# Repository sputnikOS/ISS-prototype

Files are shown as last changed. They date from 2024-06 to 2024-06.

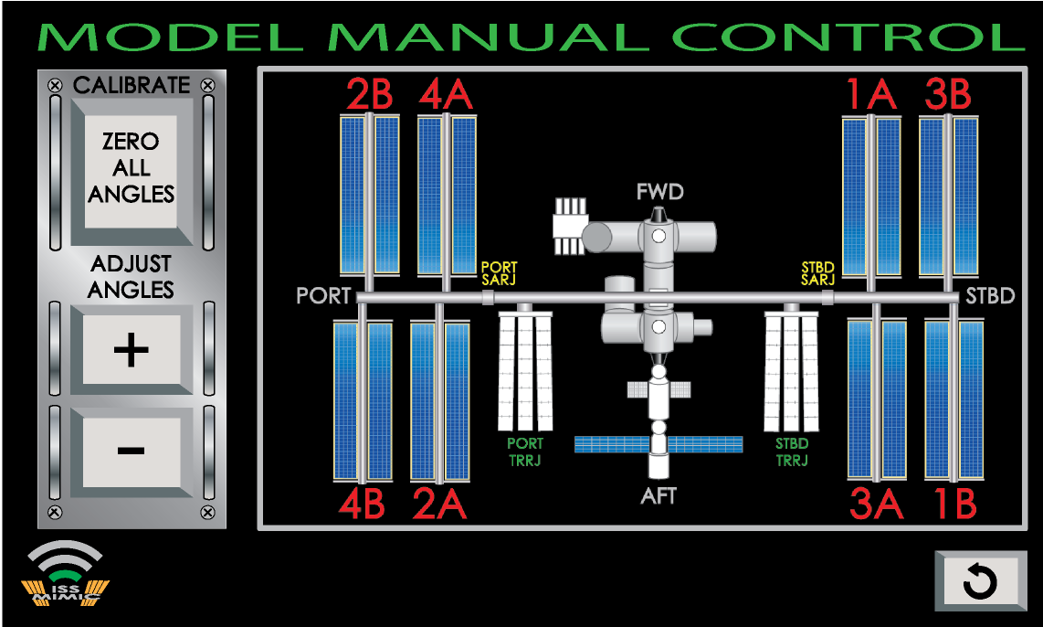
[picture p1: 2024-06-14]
Pi/imgs/calibrate/CalibrateExample.png

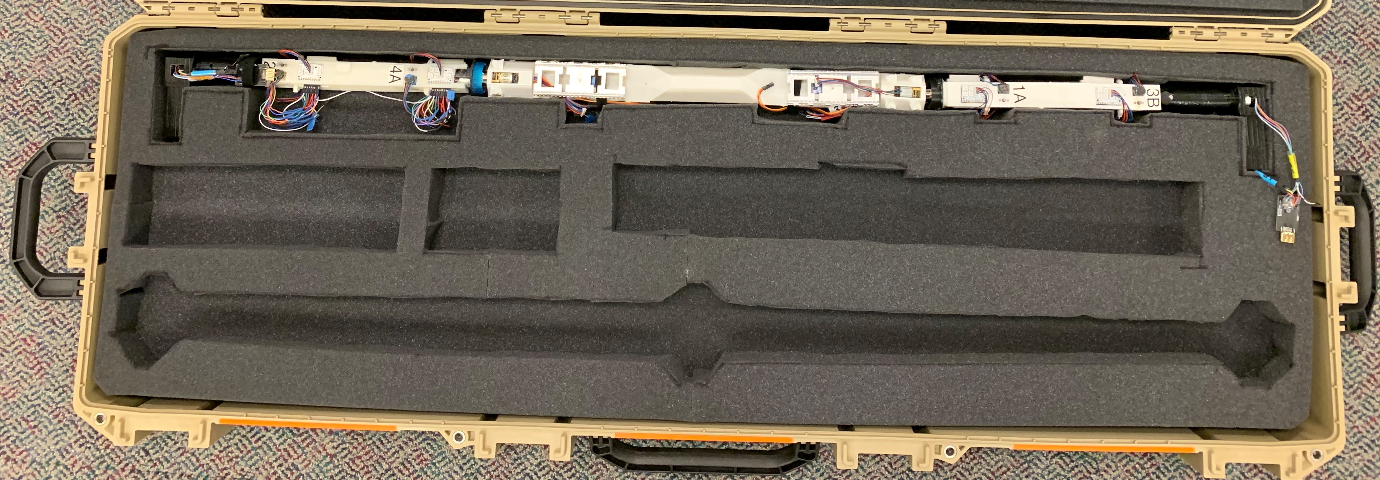
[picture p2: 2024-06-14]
Wiki/Images/Case_4_Main_Electronic_In.JPG

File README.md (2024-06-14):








Welcome to the ISS Mimic project repository! We are developing a 3D printed model of the International Space Station that uses the actual ISS live telemetry to mimic the actual positioning of the ISS solar arrays and radiators! We are also developing tools to visualize all of the ISS public telemetry in informative ways! Join our discord to provide feedback, ask questions, or get involved! 

https://discord.gg/zPKyE6hBSe

We are always looking for people to help with the coding of our raspberry pi telemetry display program, the telemetry website, the creation of ISS CAD models, general project ideas, etc... 

If you want to build your own ISS Mimic, or just want to use the ISS telemetry in your own application, we are more than happy to help. 

Check out our youtube video:

ISS MIMIC! (https://www.youtube.com/watch?v=W9iZBjzOEEQ)

ISS MIMIC!

The International Space Station is constantly downlinking data (telemetry) for Mission Control to monitor. Several years ago, NASA provided some of the data to the public in order to spur interest in the ISS and space exploration under the (now defunct) ISSlive project using the lightstreamer service (http://demos.lightstreamer.com/ISSLive/). We saw this project and wanted to expand on its potential. Since the development of isslive.com, some more data was added to the public feed and was, sadly, never incorporated into the website. The current total epic and all inclusive list of public telemetry can be seen at our page here https://iss-mimic.github.io/Mimic/ and in an even cooler format here https://iss-mimic.github.io/Mimic/dashboard.html Sadly, ISSlive.com is no longer maintained, but thanks largely in part to our efforts, the telemetry is still being provided to the public through the same lightstreamer connection. 

You can find info on installing our (still heavily in development but with some pretty cool working features now) custom ISS telemetry display program here: https://github.com/ISS-Mimic/Mimic/wiki/Build-Instruction%3A-Mimic-Software-Setup-Instructions

The telemetry is awesome in and of itself. But we wanted to do something more with the data, using it to drive software and hardware. Software - running a Raspberry Pi, we want to display all of the telemetry in an interesting and informative manner, enabling visualization of more than just boring numbers. Hardware - using Arduino related microcontrollers, receiving data from the Raspberry Pi, we want to control a 3D-printed model of the ISS and make it exactly match up with the actual ISS in real time. All of the solar arrays, radiators, and outboard truss will be able to rotate to match the ISS joint angles.

Stuff that moves

The project is still a work in progress. We have a fully functioning model that works with all 12 motors turning correctly and able to sync with live data. However, we want to increase the fidelity. Our low-fidelity model is completely finished and available here: [STL Files](https://github.com/ISS-Mimic/Mimic/tree/main/3D_Printing). We are still working on the high fidelity upgrade (help us!) and trying to make the ISS look as detailed as possible while still being printable. The software is still a work in progress, too. But from the standpoint of receiving telemetry and transmitting it to the Arduinos, the basic functionality is finished. The finishing touches on the software are all for visualizing the telemetry.

Functional but not pretty model!

DISCLAIMER - We are not professional programmers. We are just a group of dedicated ISS program employees and enthusiasts trying to share our love of the space program through this awesome project. All the code maintained here was created to work toward our specific goal, and much of it was using languages that none of us had used before. You may find the structure, style, and lack of comments to be completely novice and infuriating. You may scream out in frustration, laugh in disgust, or even weep at the obfuscated nonsense appearing before your eyes. 

That said, feel free to improve upon our caffeine-induced, late-night, insanity-plagued programming madness or even just scrap it all and make something better using our ideas.

Check out the wiki for more information.

You can view a video showing some of our project here:https://youtu.be/W9iZBjzOEEQ. Here's an older video: https://www.youtube.com/watch?v=sbdHXjDQ-U8 .

The software is pretty cool and provides even more in-depth functionality than isslive.com. We'll be adding videos and pictures soon to show off the software capabilities.

# Status/Priorities
We are currently focused on refining the CAD model and splitting out all the STL files for printing. All of the STL files currently in this repo are likely outdated or currently changing. We will also release the raw CAD once finished.

We are also working on finishing the software.

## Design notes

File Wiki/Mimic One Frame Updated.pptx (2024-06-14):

## Mimic One Frame Build Instruction (Example)

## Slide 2

FWD

2020 Vertical Supports (4)

Extruded 2040 Base

2020 Frame Supports (6)

Support Rods with Base (3)

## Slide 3

Step 1: Attach Frame Supports to 2040 Base (6 places)
2 small L-brackets each support, 2 Button Hex Screws each small L-bracket

Measurements are from centerline to centerline

2020 Frame Supports (6)

Frame Supports attached to 2040 Base by 2 small L-brackets using Button Hex Screws

Extruded 2040 Base

~610mm

~610mm

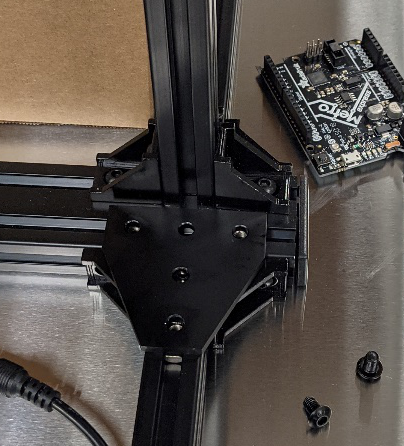
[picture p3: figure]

L-brackets

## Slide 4

Step 1a: Cut Rubber Strips for Frame Supports (6 places) and 2040 Base (both grooves)
Install Rubber Strips in the underside grooves of Frame Supports and 2040 Base.

The Rubber Strip provides friction with the table and to fill the space between the table and the Rubber Feet on the end of the Frame Supports.

2020 Frame Supports (6)

Extruded 2040 Base (both grooves)

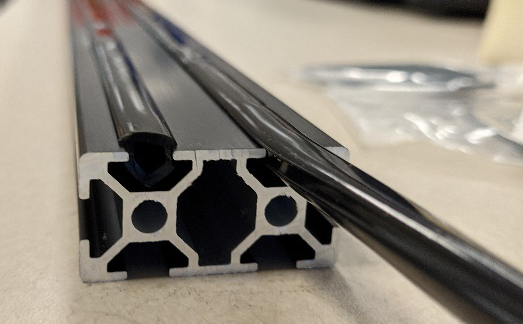
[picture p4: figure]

2040 Base shown upside down

Underside Groove

Rubber Strip

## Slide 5

Step 2: Install T-Plates on end Frame Supports in the rear groove of the 2040 (2 places)
1 T-plate per end Frame Support, 5 Button Hex Screws and T-nuts on each T-plate

2020 Frame Supports (6)

Frame Supports attached to 2040 Base by 2 small L-brackets and 1 T-plate using Button Hex Screws

Extruded 2040 Base

T-plate

L-brackets

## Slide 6

Step 3: Install T-Plates on center Frame Supports – one in forward groove, one in rear groove (2 places)
1 T-plate per center Frame Support, 5 Button Hex Screws and T-nuts on each T-plate

FWD

2020 Frame Supports (6)

Extruded 2040 Base

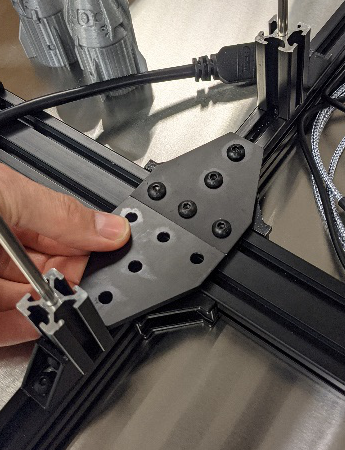
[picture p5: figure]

T-plates

Forward Groove in 2040

Rear Groove in 2040

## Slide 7

Vertical Supports (without T-plates) attached to forward groove with 2 small
L-brackets using
Button Hex screws

2020 Vertical Supports (4)

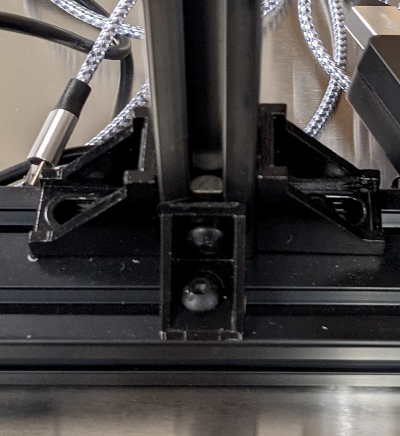
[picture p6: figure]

L-brackets

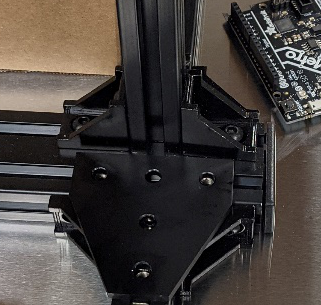
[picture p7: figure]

L-brackets

Vertical Supports attached to forward groove on 2040 Base by 2 small L-brackets using Button Hex Screws

Measurements are centerline to centerline.
Need to update: outside dimensions should be the same.

FWD

446mm

433mm

347mm

Extruded 2040 Base

Step 4: Attach Vertical Supports to forward groove in 2040 Base (4 places)
2 small L-brackets each support, 2 Button Hex Screws each small L-bracket

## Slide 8

Vertical Supports (without T-plates) attached to forward groove with 2 small
L-brackets and 1
L-bracket anchored in rear groove

2020 Vertical Supports (4)

Step 5: Add 1 large L-bracket anchored in rear groove in 2040 Base on center supports(2 places)
1 large L-bracket each support, 2 Button Hex Screws each small L-bracket

FWD

Extruded 2040 Base

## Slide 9

Step 6: Support Rod Bases on center Frame Supports (3 places)
1 large L-bracket per Support Rod Base, 2 Button Hex Screws each L-bracket

2020 Frame Supports (6)

160mm

243mm

Extruded 2040 Base

L-brackets

Vertical 2020 is flush
with end of the horizontal 2020

Support Rods with Base (3)

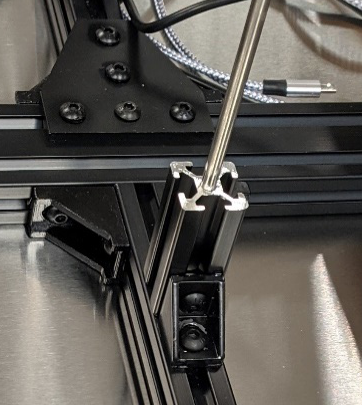
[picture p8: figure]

Support Rod Base attached to 2020 Frame Support by 1 large
L-bracket using Button Hex Screws

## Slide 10

Step 7: Install Rubber Feet on Support Rod Bases (3 places)
Rubber Feet finish off ends of extruded Support Rod Bases and provide additional support with rods

Note, a cut will need to be made or a small hole drilled to allow Support Rod to pass through – hole must be smaller than rod to provide friction for extra stability

2020 Frame Supports (6)

Extruded 2040 Base

Add new photo with rubber

Rubber Feet on Support Rod Base

Support Rods with Base (3)

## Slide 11

Step 8: Insert Support Rods in Support Rod Bases (3 places)
Support Rod will drop down into groove of Frame Support

2020 Frame Supports (6)

Extruded 2040 Base

Add new photo with rubber

Support Rod inserted through Rubber Feet into Support Rod Base

Support Rods with Base (3)

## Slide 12

Step 9: Install Rubber Feet on Frame Supports (6 places)
Rubber Feet finish off ends of Frame Supports and provide friction with table

2020 Frame Supports (6)

Extruded 2040 Base

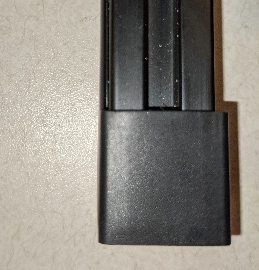
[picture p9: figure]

Support Rods with Base (3)

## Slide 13

Step 10: Install End Caps on 2040 Base ends (2 places)
End Caps finish off ends of 2040 Base

Extruded 2040 Base

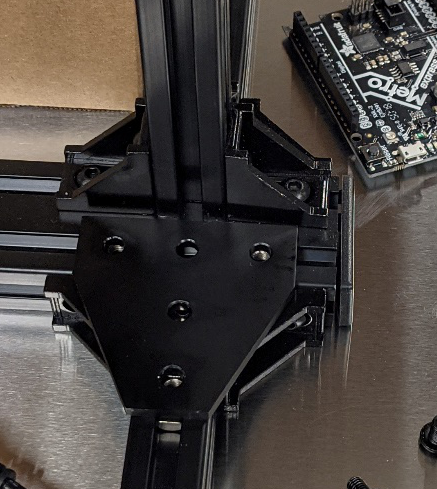
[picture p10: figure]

End Cap (2) inserted into end of 2040 Base

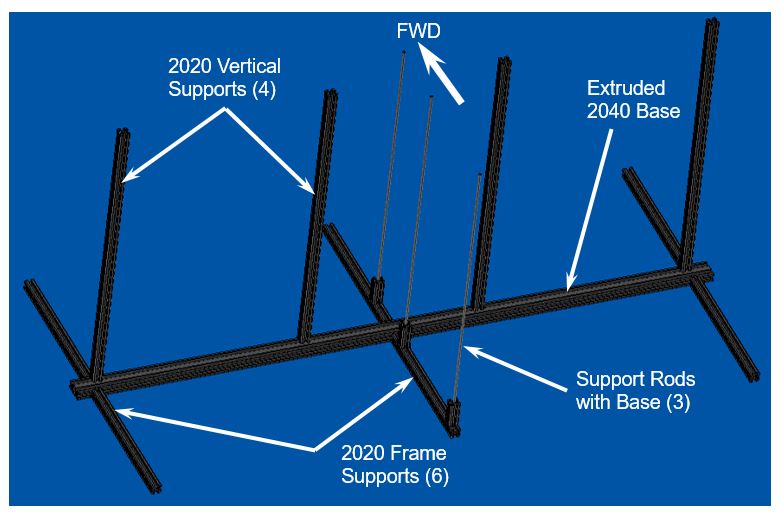
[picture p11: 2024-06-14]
Wiki/Images/FrameOverview.JPG

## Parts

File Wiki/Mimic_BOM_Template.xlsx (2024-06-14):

 |  |  |  |  |  |  |  | output string - copy everything below in this column for the markdown file |  |  |  |  |  |  |  |  | concats
 |  |  |  |  |  |  |  | ### Raspberry Pi / Mimic Control Unit
 |  |  |  |  |  |  |  | | **Part** | **Quantity** | **Cost Per Unit** | **Total Cost** | **URL** | **Notes** | **Image**
Part | Quantity | Cost Per Unit | Total Cost | Part URL Name | Part URL | Notes | Image URL | | --- | :--: | :--: | :--: | --- | --- | ---
4GB Raspberry Pi 4 | 1 | $67.79 | $67.79 | Amazon | https://www.amazon.com/dp/B07TC2BK1X | Might work with the 1GB/2GB versions but not guaranteed | https://images-na.ssl-images-amazon.com/images/I/71RJj8SmQGL._SL1500_.jpg | | 4GB Raspberry Pi 4 | 1 | $67.79 | $67.79 | [Amazon](https://www.amazon.com/dp/B07TC2BK1X) | Might work with the 1GB/2GB versions but not guaranteed | <img src="https://images-na.ssl-images-amazon.com/images/I/71RJj8SmQGL._SL1500_.jpg" width="200">
Power Supply | 1 | $9.99 | $9.99 | Amazon | https://www.amazon.com/gp/product/B097P2NLVH/ | Need at least 2.4 amp power supply | https://m.media-amazon.com/images/I/610tc+KJ17S._AC_SL1500_.jpg | | Power Supply | 1 | $9.99 | $9.99 | [Amazon](https://www.amazon.com/gp/product/B097P2NLVH/) | Need at least 2.4 amp power supply | <img src="https://m.media-amazon.com/images/I/610tc+KJ17S._AC_SL1500_.jpg" width="200">
MicroSD Card | 1 | $8.98 | $8.98 | Amazon | https://www.amazon.com/SanDisk-Ultra-microSDXC-Memory-Adapter/dp/B073JWXGNT | Recommend 32GB, you'll also need a microSD card reader | https://images-na.ssl-images-amazon.com/images/I/81ClkOh2gpL._SL1500_.jpg | | MicroSD Card | 1 | $8.98 | $8.98 | [Amazon](https://www.amazon.com/SanDisk-Ultra-microSDXC-Memory-Adapter/dp/B073JWXGNT) | Recommend 32GB, you'll also need a microSD card reader | <img src="https://images-na.ssl-images-amazon.com/images/I/81ClkOh2gpL._SL1500_.jpg" width="200">
Raspberry Pi Official Touchscreen | 1 | $92.81 | $92.81 | Amazon | https://www.amazon.com/Raspberry-Pi-7-Touchscreen-Display/dp/B0153R2A9I/ | Possible to use other screens but the program was designed for this one | https://images-na.ssl-images-amazon.com/images/I/51Fju0ie9sL._SL1000_.jpg | | Raspberry Pi Official Touchscreen | 1 | $92.81 | $92.81 | [Amazon](https://www.amazon.com/Raspberry-Pi-7-Touchscreen-Display/dp/B0153R2A9I/) | Possible to use other screens but the program was designed for this one | <img src="https://images-na.ssl-images-amazon.com/images/I/51Fju0ie9sL._SL1000_.jpg" width="200">
Raspberry Pi/Touchscreen Case (optional) | 1 | $29.99 | $29.99 | Amazon | https://www.amazon.com/SmartiPi-Touch-Official-Raspberry-Touchscreen/dp/B07WXK38YM/ | This is the best Raspi Case but again not strictly required | https://images-na.ssl-images-amazon.com/images/I/71P7ThIhIRL._SL1500_.jpg | | Raspberry Pi/Touchscreen Case (optional) | 1 | $29.99 | $29.99 | [Amazon](https://www.amazon.com/SmartiPi-Touch-Official-Raspberry-Touchscreen/dp/B07WXK38YM/) | This is the best Raspi Case but again not strictly required | <img src="https://images-na.ssl-images-amazon.com/images/I/71P7ThIhIRL._SL1500_.jpg" width="200">
4-Port Powered USB Hub | 1 | $19.99 | $19.99 | Amazon | https://www.amazon.com/gp/product/B00TPMEOYM/ | Any powered hub should work, but this is the one we for which we've designed a mount | https://m.media-amazon.com/images/I/71fOD0-BRQL._AC_SL1500_.jpg | | 4-Port Powered USB Hub | 1 | $19.99 | $19.99 | [Amazon](https://www.amazon.com/gp/product/B00TPMEOYM/) | Any powered hub should work, but this is the one we for which we've designed a mount | <img src="https://m.media-amazon.com/images/I/71fOD0-BRQL._AC_SL1500_.jpg" width="200">
USB-A to USB-Micro B data cables | 1 | $11.99 | $11.99 | Amazon | https://www.amazon.com/gp/product/B011KLFERG/ | Four cables required. You can use old phone cables, but make sure they support data transfer, not just charging | https://m.media-amazon.com/images/I/81z7vkDJTdL._AC_SL1500_.jpg | | USB-A to USB-Micro B data cables | 1 | $11.99 | $11.99 | [Amazon](https://www.amazon.com/gp/product/B011KLFERG/) | Four cables required. You can use old phone cables, but make sure they support data transfer, not just charging | <img src="https://m.media-amazon.com/images/I/81z7vkDJTdL._AC_SL1500_.jpg" width="200">
Mini Wireless Keyboard + Mouse (optional) | 1 | $29.95 | $29.95 | Amazon | https://www.amazon.com/gp/product/B011KPIZ9G/ | Use whatever mouse + keyboard you like, we like how this is a mouse and keyboard, portable and only uses one USB port | https://images-na.ssl-images-amazon.com/images/I/41YUr5YjuFL._AC_.jpg | | Mini Wireless Keyboard + Mouse (optional) | 1 | $29.95 | $29.95 | [Amazon](https://www.amazon.com/gp/product/B011KPIZ9G/) | Use whatever mouse + keyboard you like, we like how this is a mouse and keyboard, portable and only uses one USB port | <img src="https://images-na.ssl-images-amazon.com/images/I/41YUr5YjuFL._AC_.jpg" width="200">
USB Battery Pack (optional) | 1 | $49.95 | $49.95 | Amazon | https://www.amazon.com/Anker-PowerCore-Technology-High-Capacity-Compatible/dp/B07S829LBX/ | If you want to have a portable power option for the Raspberry Pi Station, this is a good option | https://images-na.ssl-images-amazon.com/images/I/71PYhWFaWEL._AC_SL1500_.jpg | | USB Battery Pack (optional) | 1 | $49.95 | $49.95 | [Amazon](https://www.amazon.com/Anker-PowerCore-Technology-High-Capacity-Compatible/dp/B07S829LBX/) | If you want to have a portable power option for the Raspberry Pi Station, this is a good option | <img src="https://images-na.ssl-images-amazon.com/images/I/71PYhWFaWEL._AC_SL1500_.jpg" width="200">
 |  |  |  |  |  |  |  | | **Subtotal** | **Subtotal + Keyboard & Battery**
 |  |  |  |  |  |  |  | | :---: | :---:
 |  | $241.54 | $321.44 |  |  |  |  | | $241.54 | $321.44
 |  |  |  |  |  |  |  | ### Essential Parts
 |  |  |  |  |  |  |  | | **Part** | **Quantity** | **Cost Per Unit** | **Total Cost** | **URL** | **Notes** | **Image**
Part | Quantity | Cost Per Unit | Total Cost | Part URL Name | Part URL | Notes | Image URL | | --- | :--: | :--: | :--: | --- | --- | ---
175 RPM Micro Gear Motor w/Encoder | 10 | $19.99 | $199.90 | Amazon | https://www.amazon.com/175-RPM-Micro-Gearmotor-Encoder/dp/B0195C9GSU | Motor for SARJs + BGAs | https://github.com/ISS-Mimic/Mimic/blob/main/Wiki/Images/DCmotor.png | | 175 RPM Micro Gear Motor w/Encoder | 10 | $19.99 | $199.9 | [Amazon](https://www.amazon.com/175-RPM-Micro-Gearmotor-Encoder/dp/B0195C9GSU) | Motor for SARJs + BGAs | <img src="https://github.com/ISS-Mimic/Mimic/blob/main/Wiki/Images/DCmotor.png" width="200">
Motor mount screws | 1 | $9.54 | $9.54 | McMasterCarr | https://www.mcmaster.com/92010A779/ | Mounts motors in place. M1.6x4mm flat head hex screw (100 pack). Total of 20 screws required. | https://github.com/ISS-Mimic/Mimic/blob/main/Wiki/Images/mmc_screw.png | | Motor mount screws | 1 | $9.54 | $9.54 | [McMasterCarr](https://www.mcmaster.com/92010A779/) | Mounts motors in place. M1.6x4mm flat head hex screw (100 pack). Total of 20 screws required. | <img src="https://github.com/ISS-Mimic/Mimic/blob/main/Wiki/Images/mmc_screw.png" width="200">
Couplers to Mount Solar Arrays on the motors | 1 | $10.99 | $10.99 | Amazon | https://www.amazon.com/Befenybay-Connector-Copper-Flexible-Coupling/dp/B07VFFJBVH/ | (8 Pcs) 3mm to 3mm Brass Connector Copper | https://images-na.ssl-images-amazon.com/images/I/71Gfh5ie8ML._AC_SX679_.jpg | | Couplers to Mount Solar Arrays on the motors | 1 | $10.99 | $10.99 | [Amazon](https://www.amazon.com/Befenybay-Connector-Copper-Flexible-Coupling/dp/B07VFFJBVH/) | (8 Pcs) 3mm to 3mm Brass Connector Copper | <img src="https://images-na.ssl-images-amazon.com/images/I/71Gfh5ie8ML._AC_SX679_.jpg" width="200">
Replacement Set Screws for Solar Array Couplers | 1 | $3.50 | $3.50 | McMaster | https://www.mcmaster.com/92605A100/ | M3 x 6mm Long Stainless Steel Flat-Tip Set Screw (Pkg of 25) | https://github.com/ISS-Mimic/Mimic/blob/main/Wiki/Images/mmc_setscrew.png | | Replacement Set Screws for Solar Array Couplers | 1 | $3.5 | $3.5 | [McMaster](https://www.mcmaster.com/92605A100/) | M3 x 6mm Long Stainless Steel Flat-Tip Set Screw (Pkg of 25) | <img src="https://github.com/ISS-Mimic/Mimic/blob/main/Wiki/Images/mmc_setscrew.png" width="200">
Pinion Gear to work with printed SARJ Ring | 2 | $9.70 | $19.40 | Amazon | https://www.amazon.com/Traxxas-3942X-Hardened-12-Tooth-Pinion/dp/B078KFCN72 | Traxxas 3942X 12-T Pinion Gear, 32P | https://m.media-amazon.com/images/I/41lWRhK7rWS._AC_SL1400_.jpg | | Pinion Gear to work with printed SARJ Ring | 2 | $9.7 | $19.4 | [Amazon](https://www.amazon.com/Traxxas-3942X-Hardened-12-Tooth-Pinion/dp/B078KFCN72) | Traxxas 3942X 12-T Pinion Gear, 32P | <img src="https://m.media-amazon.com/images/I/41lWRhK7rWS._AC_SL1400_.jpg" width="200">
Slip Ring | 4 | $21.00 | $84.00 | Amazon | https://www.amazon.com/GeeBat-Capsule-Electrical-CIRCUITSx2A-equipment/dp/B01N63E1N3 | Slip Ring - 12 Wires with Flange | https://images-na.ssl-images-amazon.com/images/I/71P8F3tKd3L._AC_SX679_.jpg | | Slip Ring | 4 | $21 | $84 | [Amazon](https://www.amazon.com/GeeBat-Capsule-Electrical-CIRCUITSx2A-equipment/dp/B01N63E1N3) | Slip Ring - 12 Wires with Flange | <img src="https://images-na.ssl-images-amazon.com/images/I/71P8F3tKd3L._AC_SX679_.jpg" width="200">
Motor Driver Shield | 3 | $23.99 | $71.97 | Amazon | https://www.amazon.com/gp/product/B073SP76MC/ | HiLetgo TB6612 Mosfet for Arduino Motor Shield | https://m.media-amazon.com/images/I/61w0lRDnX5L._AC_SL1010_.jpg | | Motor Driver Shield | 3 | $23.99 | $71.97 | [Amazon](https://www.amazon.com/gp/product/B073SP76MC/) | HiLetgo TB6612 Mosfet for Arduino Motor Shield | <img src="https://m.media-amazon.com/images/I/61w0lRDnX5L._AC_SL1010_.jpg" width="200">
Adafruit Metro M0 | 4 | $36.95 | $147.80 | Amazon | https://www.amazon.com/Adafruit-3505-Metro-Express-CircuitPython/dp/B071P145RG/ | Adafruit (PID 3505 Metro M0 Express - Designed for CircuitPython - ATSAMD21G18 | https://images-na.ssl-images-amazon.com/images/I/811K-LHnsoL._AC_SL1200_.jpg | | Adafruit Metro M0 | 4 | $36.95 | $147.8 | [Amazon](https://www.amazon.com/Adafruit-3505-Metro-Express-CircuitPython/dp/B071P145RG/) | Adafruit (PID 3505 Metro M0 Express - Designed for CircuitPython - ATSAMD21G18 | <img src="https://images-na.ssl-images-amazon.com/images/I/811K-LHnsoL._AC_SL1200_.jpg" width="200">
Servo Motors for Radiators | 1 | $9.99 | $9.99 | Amazon | https://www.amazon.com/Micro-Servos-Helicopter-Airplane-Controls/dp/B07MLR1498/ | TowerPro SG90 Servo (2 required, 4 in this pack) | https://images-na.ssl-images-amazon.com/images/I/61EX8cfTXRL._AC_SL1200_.jpg | | Servo Motors for Radiators | 1 | $9.99 | $9.99 | [Amazon](https://www.amazon.com/Micro-Servos-Helicopter-Airplane-Controls/dp/B07MLR1498/) | TowerPro SG90 Servo (2 required, 4 in this pack) | <img src="https://images-na.ssl-images-amazon.com/images/I/61EX8cfTXRL._AC_SL1200_.jpg" width="200">
Jumper Wires for Motor and Mimic Shields | 1 | $6.98 | $6.98 | Amazon | https://www.amazon.com/gp/product/B01EV70C78/ (https://smile.amazon.com/gp/product/B01EV70C78/) | 20cm Assorted Breadboard Jumper Wires | https://m.media-amazon.com/images/I/81lyrrBqMIL._AC_SL1500_.jpg | | Jumper Wires for Motor and Mimic Shields | 1 | $6.98 | $6.98 | [Amazon](https://www.amazon.com/gp/product/B01EV70C78/) | 20cm Assorted Breadboard Jumper Wires | <img src="https://m.media-amazon.com/images/I/81lyrrBqMIL._AC_SL1500_.jpg" width="200">
12V/5A Power Supply for Motors | 1 | $12.99 | $12.99 | Amazon | https://www.amazon.com/gp/product/B01461MOGQ (https://smile.amazon.com/gp/product/B01461MOGQ) | LEDMO Power Supply | https://m.media-amazon.com/images/I/51a0PcZlVkL._AC_.jpg | | 12V/5A Power Supply for Motors | 1 | $12.99 | $12.99 | [Amazon](https://www.amazon.com/gp/product/B01461MOGQ) | LEDMO Power Supply | <img src="https://m.media-amazon.com/images/I/51a0PcZlVkL._AC_.jpg" width="200">
Inline On/Off Switch (Optional) | 1 | $9.99 | $9.99 | Amazon | https://www.amazon.com/AWADUO-Extension-Adapter-Connector-Security/dp/B0B4638FG | JEEUE 12V Power DC Male to Female Cable with On/Off Switch | https://m.media-amazon.com/images/I/51istd+aMsL._SL1000_.jpg | | Inline On/Off Switch (Optional) | 1 | $9.99 | $9.99 | [Amazon](https://www.amazon.com/AWADUO-Extension-Adapter-Connector-Security/dp/B0B4638FG) | JEEUE 12V Power DC Male to Female Cable with On/Off Switch | <img src="https://m.media-amazon.com/images/I/51istd+aMsL._SL1000_.jpg" width="200">
DC Power Splitter Cable | 1 | $8.99 | $8.99 | Amazon | https://www.amazon.com/gp/product/B06Y5G3CMJ (https://smile.amazon.com/gp/product/B06Y5G3CMJ) | DZYDZR 3pcs 5.5mm x 2.1mm Y Splitter Cable 1 Female to 3 Male Splitter | https://m.media-amazon.com/images/I/61rz64AJ-KL._AC_SL1000_.jpg | | DC Power Splitter Cable | 1 | $8.99 | $8.99 | [Amazon](https://www.amazon.com/gp/product/B06Y5G3CMJ) | DZYDZR 3pcs 5.5mm x 2.1mm Y Splitter Cable 1 Female to 3 Male Splitter | <img src="https://m.media-amazon.com/images/I/61rz64AJ-KL._AC_SL1000_.jpg" width="200">
DC Power Plug Pigtail | 1 | $8.43 | $8.43 | Amazon | https://www.amazon.com/gp/product/B01M0EAR9N (https://smile.amazon.com/gp/product/B01M0EAR9N) | DC Power Plug Pigtail Cable (Female Power Plug Pigtail Cable / 19.68 inches/Pack of 10) | https://m.media-amazon.com/images/I/71WZivU7NpL._AC_SL1500_.jpg | | DC Power Plug Pigtail | 1 | $8.43 | $8.43 | [Amazon](https://www.amazon.com/gp/product/B01M0EAR9N) | DC Power Plug Pigtail Cable (Female Power Plug Pigtail Cable / 19.68 inches/Pack of 10) | <img src="https://m.media-amazon.com/images/I/71WZivU7NpL._AC_SL1500_.jpg" width="200">
Velcro Cable Ties (optional) | 1 | $6.99 | $6.99 | Amazon | https://www.amazon.com/gp/product/B00O9VKVFK (https://smile.amazon.com/gp/product/B00O9VKVFK) | Attmu 50 PCS Reusable Fastening Cable Ties | https://m.media-amazon.com/images/I/719z+1KonvL._AC_SL1500_.jpg | | Velcro Cable Ties (optional) | 1 | $6.99 | $6.99 | [Amazon](https://www.amazon.com/gp/product/B00O9VKVFK) | Attmu 50 PCS Reusable Fastening Cable Ties | <img src="https://m.media-amazon.com/images/I/719z+1KonvL._AC_SL1500_.jpg" width="200">
HDMI Cables (Generic) | 3 | $10.99 | $32.97 | Amazon | https://www.amazon.com/gp/product/B07LFN7CX6 | Any standard HDMI cable should work | https://m.media-amazon.com/images/I/610Y4RHIzRL._AC_SL1200_.jpg | | HDMI Cables (Generic) | 3 | $10.99 | $32.97 | [Amazon](https://www.amazon.com/gp/product/B07LFN7CX6) | Any standard HDMI cable should work | <img src="https://m.media-amazon.com/images/I/610Y4RHIzRL._AC_SL1200_.jpg" width="200">
 |  |  |  |  |  |  |  | | **Subtotal**
 |  |  |  |  |  |  |  | | :---:
 |  |  | $644.43 |  |  |  |  | | $644.43
 |  |  |  |  |  |  |  | ### Modelling (3D Printing/Module Connections/Aesthetics)
 |  |  |  |  |  |  |  | | **Part** | **Quantity** | **Cost Per Unit** | **Total Cost** | **URL** | **Notes** | **Image**
Part | Quantity | Cost Per Unit | Total Cost | Part URL Name | Part URL | Notes | Image URL | | --- | :--: | :--: | :--: | --- | --- | ---
3D Printer PLA Filament | 1 | $24.99 | $24.99 | Amazon | https://www.amazon.com/gp/product/B0B2NZZXLX | 3D Printer Filament, Polymaker White - be sure to get the proper diameter filament for your printer (feel free to use whatever filament) | https://m.media-amazon.com/images/I/71etInNZiSL._AC_SL1500_.jpg | | 3D Printer PLA Filament | 1 | $24.99 | $24.99 | [Amazon](https://www.amazon.com/gp/product/B0B2NZZXLX) | 3D Printer Filament, Polymaker White - be sure to get the proper diameter filament for your printer (feel free to use whatever filament) | <img src="https://m.media-amazon.com/images/I/71etInNZiSL._AC_SL1500_.jpg" width="200">
Ring Magnets for Module Connecting - lightweight | 60 | $0.52 | $31.20 | KJ Magnetics | https://www.kjmagnetics.com/proddetail.asp?prod=R841 | ½”OD x 1/4”ID x 1/16”thick ring magnets | https://www.kjmagnetics.com/prodimages2/1280/R841one.jpg | | Ring Magnets for Module Connecting - lightweight | 60 | $0.52 | $31.2 | [KJ Magnetics](https://www.kjmagnetics.com/proddetail.asp?prod=R841) | ½”OD x 1/4”ID x 1/16”thick ring magnets | <img src="https://www.kjmagnetics.com/prodimages2/1280/R841one.jpg" width="200">
Ring Magnets for Module Connecting - Heavyweight | 10 | $1.04 | $10.40 | KJ Magnetics | https://www.kjmagnetics.com/proddetail.asp?prod=R842-N52 | ½”OD x 1/4”ID x 1/8” thick ring magnets | https://www.kjmagnetics.com/prodimages2/1280/R842-N52one.jpg | | Ring Magnets for Module Connecting - Heavyweight | 10 | $1.04 | $10.4 | [KJ Magnetics](https://www.kjmagnetics.com/proddetail.asp?prod=R842-N52) | ½”OD x 1/4”ID x 1/8” thick ring magnets | <img src="https://www.kjmagnetics.com/prodimages2/1280/R842-N52one.jpg" width="200">
Cylinder Magnets for TBD | 2 | $1.40 | $2.80 | KJ Magnetics | https://www.kjmagnetics.com/proddetail.asp?prod=D12-N52 | 1/16”diam x 1/8” thick cylinder magnets | https://www.kjmagnetics.com/prodimages2/1280/D12-N52one.jpg | | Cylinder Magnets for TBD | 2 | $1.4 | $2.8 | [KJ Magnetics](https://www.kjmagnetics.com/proddetail.asp?prod=D12-N52) | 1/16”diam x 1/8” thick cylinder magnets | <img src="https://www.kjmagnetics.com/prodimages2/1280/D12-N52one.jpg" width="200">
Support Rods for Inboard Truss Segment | 2 | $2.54 | $5.08 | McMaster | https://www.mcmaster.com/98861A040/ | M3 Steel Threaded Rod, 1-m Long | https://github.com/ISS-Mimic/Mimic/blob/main/Wiki/Images/mmc_nut.png | | Support Rods for Inboard Truss Segment | 2 | $2.54 | $5.08 | [McMaster](https://www.mcmaster.com/98861A040/) | M3 Steel Threaded Rod, 1-m Long | <img src="https://github.com/ISS-Mimic/Mimic/blob/main/Wiki/Images/mmc_nut.png" width="200">
M3 Locknuts | 1 | $4.65 | $4.65 | McMaster | https://www.mcmaster.com/90576A102/ | M3 Steel Nylon-Insert Locknut (Pkg 100) | https://github.com/ISS-Mimic/Mimic/blob/main/Wiki/Images/mmc_threadedrod.png | | M3 Locknuts | 1 | $4.65 | $4.65 | [McMaster](https://www.mcmaster.com/90576A102/) | M3 Steel Nylon-Insert Locknut (Pkg 100) | <img src="https://github.com/ISS-Mimic/Mimic/blob/main/Wiki/Images/mmc_threadedrod.png" width="200">
Bamboo Skewers for attaching module halves | 1 | $5.99 | $5.99 | Amazon | https://www.amazon.com/Appetiser-Cocktail-Chocolate-Fountain-Barbecue/dp/B07MY7XVB1/ | HOPELF 6" Natural Bamboo Skewers, Φ=4mm (100 pcs) | https://m.media-amazon.com/images/I/61MhlR2cAtL._AC_SL1500_.jpg | | Bamboo Skewers for attaching module halves | 1 | $5.99 | $5.99 | [Amazon](https://www.amazon.com/Appetiser-Cocktail-Chocolate-Fountain-Barbecue/dp/B07MY7XVB1/) | HOPELF 6" Natural Bamboo Skewers, Φ=4mm (100 pcs) | <img src="https://m.media-amazon.com/images/I/61MhlR2cAtL._AC_SL1500_.jpg" width="200">
Cyanoacrylate Glue | 1 | $9.49 | $9.49 | Amazon | https://www.amazon.com/Gorilla-105801-Super-1-Pack-Clear/dp/B08QR2XRKD | Gorilla Super Glue Gel (any "superglue" should work) | https://m.media-amazon.com/images/I/81kAtvCkeBS._AC_SL1500_.jpg | | Cyanoacrylate Glue | 1 | $9.49 | $9.49 | [Amazon](https://www.amazon.com/Gorilla-105801-Super-1-Pack-Clear/dp/B08QR2XRKD) | Gorilla Super Glue Gel (any "superglue" should work) | <img src="https://m.media-amazon.com/images/I/81kAtvCkeBS._AC_SL1500_.jpg" width="200">
Metallic Gold Vinyl for Solar Arrays | 2 | $11.99 | $23.98 | Amazon | https://www.amazon.com/gp/product/B07XZ3XY42/ | (Not Required - Aesthetic Purposes Only) Metallic Gold Vinyl (12"x6') | https://images-na.ssl-images-amazon.com/images/I/61XFjfy35XL._AC_SL1500_.jpg | | Metallic Gold Vinyl for Solar Arrays | 2 | $11.99 | $23.98 | [Amazon](https://www.amazon.com/gp/product/B07XZ3XY42/) | (Not Required - Aesthetic Purposes Only) Metallic Gold Vinyl (12"x6') | <img src="https://images-na.ssl-images-amazon.com/images/I/61XFjfy35XL._AC_SL1500_.jpg" width="200">
Ultraviolet Blue Vinyl for Solar Arrays | 2 | $12.69 | $25.38 | Amazon | https://www.amazon.com/gp/product/B07QYXHM9H/ | (Not Required - Aesthetic Purposes Only) Ultraviolet Blue Vinyl (12"x 48") | https://github.com/ISS-Mimic/Mimic/assets/58833710/6a3dd56d-9eb3-4495-8b58-9b9101e909ea | | Ultraviolet Blue Vinyl for Solar Arrays | 2 | $12.69 | $25.38 | [Amazon](https://www.amazon.com/gp/product/B07QYXHM9H/) | (Not Required - Aesthetic Purposes Only) Ultraviolet Blue Vinyl (12"x 48") | <img src="https://github.com/ISS-Mimic/Mimic/assets/58833710/6a3dd56d-9eb3-4495-8b58-9b9101e909ea" width="200">
Metallic Champagne Gold Vinyl for Solar Arrays | 2 | $12.29 | $24.58 | Amazon | https://www.amazon.com/gp/product/B088TMQ3Q6/ | (Not Required - Aesthetic Purposes Only) Ultraviolet Blue Vinyl (12"x 48") | https://github.com/ISS-Mimic/Mimic/assets/58833710/acfa16c5-2f17-4bac-9d11-94584da22d7e | | Metallic Champagne Gold Vinyl for Solar Arrays | 2 | $12.29 | $24.58 | [Amazon](https://www.amazon.com/gp/product/B088TMQ3Q6/) | (Not Required - Aesthetic Purposes Only) Ultraviolet Blue Vinyl (12"x 48") | <img src="https://github.com/ISS-Mimic/Mimic/assets/58833710/acfa16c5-2f17-4bac-9d11-94584da22d7e" width="200">
 |  |  |  |  |  |  |  | | **Subtotal** | **Subtotal + Vinyl**
 |  |  |  |  |  |  |  | | :---: | :---:
 |  | $94.60 | $168.54 |  |  |  |  | | $94.6 | $168.54
 |  |  |  |  |  |  |  | ### Frame
 |  |  |  |  |  |  |  | The frame will require black 2020 T-slot aluminum in these lengths and quantities:
 |  |  |  |  |  |  |  | * 600mm x 4
 |  |  |  |  |  |  |  | * 300mm x 6
 |  |  |  |  |  |  |  | * 50 mm x 3 (not a standard length)
 |  |  |  |  |  |  |  | * It also requires a single length of black 2040 T-slot aluminum, 1300mm long (not a standard length).
 |  |  |  |  |  |  |  | Due to the few requiring custom cuts and the way things are priced, it's easiest to order as listed here and in the BOM table below. Cuts cost $1.50 each at Zyltech.
 |  |  |  |  |  |  |  | * (Qty 1) 2000mm 2040 black T-slot aluminum, cut to 1300mm
 |  |  |  |  |  |  |  | * (Qty 5) 1000mm 2020 black T-slot aluminum, cut to (4) 600mm, (6) 300mm, (3) 50mm.
 |  |  |  |  |  |  |  | * Include a note that says "Please include cutoff pieces in shipment" so you have those for your next project.
 |  |  |  |  |  |  |  | | **Part** | **Quantity** | **Cost Per Unit** | **Total Cost** | **URL** | **Notes** | **Image**
Part | Quantity | Cost Per Unit | Total Cost | Part URL Name | Part URL | Notes | Image URL | | ---- | :--: | :--: | :--: | --- | ---- | ---
Black Frame Base 2040 Choose 2000mm (cut request on following line item) | 1 | $26.95 | $26.95 | Zyltech | https://www.zyltech.com/zyltech-2040-anodized-aluminum-extrusion-pre-cut-lengths-300mm-2000mm/ | ZYLtech 2040 Anodized Aluminum Extrusion Pre-cut lengths: choose 2000mm (later cut to 1300mm) | https://cdn11.bigcommerce.com/s-eblil3q2nd/images/stencil/1280x1280/products/870/17552/2040_final__73686__59855__46593.1679345657.jpg | | Black Frame Base 2040 Choose 2000mm (cut request on following line item) | 1 | $26.95 | $26.95 | [Zyltech](https://www.zyltech.com/zyltech-2040-anodized-aluminum-extrusion-pre-cut-lengths-300mm-2000mm/) | ZYLtech 2040 Anodized Aluminum Extrusion Pre-cut lengths: choose 2000mm (later cut to 1300mm) | <img src="https://cdn11.bigcommerce.com/s-eblil3q2nd/images/stencil/1280x1280/products/870/17552/2040_final__73686__59855__46593.1679345657.jpg" width="200">
Cut request for Black Frame Base (2040) from above: request cut to 1300mm | 1 | $1.50 | $1.50 | Zyltech | https://www.zyltech.com/aluminum-extrusion-custom-cut-service/ | Aluminum Extrusion Custom Cut Service - Request 1300mm | https://cdn11.bigcommerce.com/s-eblil3q2nd/images/stencil/1280x1280/products/403/16616/Custom_Cut_Image__80342__48138.1665254999.jpg | | Cut request for Black Frame Base (2040) from above: request cut to 1300mm | 1 | $1.5 | $1.5 | [Zyltech](https://www.zyltech.com/aluminum-extrusion-custom-cut-service/) | Aluminum Extrusion Custom Cut Service - Request 1300mm | <img src="https://cdn11.bigcommerce.com/s-eblil3q2nd/images/stencil/1280x1280/products/403/16616/Custom_Cut_Image__80342__48138.1665254999.jpg" width="200">
Frame - Supports, Black 2020 1000mm segments (cut request on following line item) | 5 | $9.95 | $49.75 | Zyltech | https://www.zyltech.com/zyltech-black-2020-aluminum-extrusion-pre-cut-lengths-300mm-2000mm/ | ZYLtech Black 2020 Aluminum Extrusion - Pre-cut lengths: choose 1000mm | https://cdn11.bigcommerce.com/s-eblil3q2nd/images/stencil/1280x1280/products/866/17522/Image_1__63675__01672__98065.1676663189.jpg | | Frame - Supports, Black 2020 1000mm segments (cut request on following line item) | 5 | $9.95 | $49.75 | [Zyltech](https://www.zyltech.com/zyltech-black-2020-aluminum-extrusion-pre-cut-lengths-300mm-2000mm/) | ZYLtech Black 2020 Aluminum Extrusion - Pre-cut lengths: choose 1000mm | <img src="https://cdn11.bigcommerce.com/s-eblil3q2nd/images/stencil/1280x1280/products/866/17522/Image_1__63675__01672__98065.1676663189.jpg" width="200">
Cut request for Black Frame Supports (2020) from above: request cut to lengths as defined in Notes | 13 | $1.50 | $19.50 | Zyltech | https://www.zyltech.com/aluminum-extrusion-custom-cut-service/ | Aluminum Extrusion Custom Cut Service - cut to (4) 600mm, (6) 300mm, (3) 50mm | https://cdn11.bigcommerce.com/s-eblil3q2nd/images/stencil/1280x1280/products/403/16616/Custom_Cut_Image__80342__48138.1665254999.jpg | | Cut request for Black Frame Supports (2020) from above: request cut to lengths as defined in Notes | 13 | $1.5 | $19.5 | [Zyltech](https://www.zyltech.com/aluminum-extrusion-custom-cut-service/) | Aluminum Extrusion Custom Cut Service - cut to (4) 600mm, (6) 300mm, (3) 50mm | <img src="https://cdn11.bigcommerce.com/s-eblil3q2nd/images/stencil/1280x1280/products/403/16616/Custom_Cut_Image__80342__48138.1665254999.jpg" width="200">
Frame Support L-brackets (small) | 1 | $6.95 | $6.95 | Zyltech | http://www.zyltech.com/12x-90-20mm-aluminum-brace-angle-bracket-for-2020-extrusion-black/ | 12x 90° 20mm Aluminum Brace/Angle Bracket for 2020 Extrusion - Black (12 per pack, total of 5 brackets needed) | https://cdn11.bigcommerce.com/s-eblil3q2nd/images/stencil/1280x1280/products/123/15917/s136714152818872222_p319_i12_w2560__66787__47030.1665254751.jpg | | Frame Support L-brackets (small) | 1 | $6.95 | $6.95 | [Zyltech](http://www.zyltech.com/12x-90-20mm-aluminum-brace-angle-bracket-for-2020-extrusion-black/) | 12x 90° 20mm Aluminum Brace/Angle Bracket for 2020 Extrusion - Black (12 per pack, total of 5 brackets needed) | <img src="https://cdn11.bigcommerce.com/s-eblil3q2nd/images/stencil/1280x1280/products/123/15917/s136714152818872222_p319_i12_w2560__66787__47030.1665254751.jpg" width="200">
Frame Support L-brackets (large) | 2 | $7.95 | $15.90 | Zyltech | http://www.zyltech.com/12x-90-2028-aluminum-corner-brace-angle-bracket-for-2020-extrusion-black/ | 12x 90° 2028 Aluminum Corner Brace/Angle Bracket for 2020 Extrusion - Black (12 per pack, total of 22 brackets needed) | https://cdn11.bigcommerce.com/s-eblil3q2nd/images/stencil/1280x1280/products/317/16468/s136714152818872222_p240_i11_w2560__48692__70496.1669392451.jpg | | Frame Support L-brackets (large) | 2 | $7.95 | $15.9 | [Zyltech](http://www.zyltech.com/12x-90-2028-aluminum-corner-brace-angle-bracket-for-2020-extrusion-black/) | 12x 90° 2028 Aluminum Corner Brace/Angle Bracket for 2020 Extrusion - Black (12 per pack, total of 22 brackets needed) | <img src="https://cdn11.bigcommerce.com/s-eblil3q2nd/images/stencil/1280x1280/products/317/16468/s136714152818872222_p240_i11_w2560__48692__70496.1669392451.jpg" width="200">
T-plate - black (for stabilization) | 4 | $1.95 | $7.80 | Zyltech | https://www.zyltech.com/2020-90-degree-t-joining-plate-black/ | 2020 90 Degree T Joining Plate - Black | https://cdn11.bigcommerce.com/s-eblil3q2nd/images/stencil/1280x1280/products/643/16947/Black_2020-2__56624__66793.1665255100.jpg | | T-plate - black (for stabilization) | 4 | $1.95 | $7.8 | [Zyltech](https://www.zyltech.com/2020-90-degree-t-joining-plate-black/) | 2020 90 Degree T Joining Plate - Black | <img src="https://cdn11.bigcommerce.com/s-eblil3q2nd/images/stencil/1280x1280/products/643/16947/Black_2020-2__56624__66793.1665255100.jpg" width="200">
Spring Loaded T-Nuts | 1 | $12.95 | $12.95 | Zyltech | https://www.zyltech.com/100x-zyltech-spring-loaded-t-nuts-for-2020-aluminum-extrusion-m4-or-m5/ | 100x ZYLtech Spring Loaded T-Nuts for 2020 Aluminum Extrusion - M5 (total of 74 nuts needed) | https://cdn11.bigcommerce.com/s-eblil3q2nd/images/stencil/500x659/products/338/16493/s136714152818872222_p271_i12_w565__84245__88962.1665254952.jpg | | Spring Loaded T-Nuts | 1 | $12.95 | $12.95 | [Zyltech](https://www.zyltech.com/100x-zyltech-spring-loaded-t-nuts-for-2020-aluminum-extrusion-m4-or-m5/) | 100x ZYLtech Spring Loaded T-Nuts for 2020 Aluminum Extrusion - M5 (total of 74 nuts needed) | <img src="https://cdn11.bigcommerce.com/s-eblil3q2nd/images/stencil/500x659/products/338/16493/s136714152818872222_p271_i12_w565__84245__88962.1665254952.jpg" width="200">
Frame Screws | 1 | $3.95 | $3.95 | Zyltech | https://www.zyltech.com/100x-zyltech-m5x8-and-m5x10-button-hex-screws/ | 100x ZYLtech M5x8 Button Hex Screws: choose M5x8 (total of 74 screws needed) | https://cdn11.bigcommerce.com/s-eblil3q2nd/images/stencil/500x659/products/332/16488/Screws_Image_2__83478__71704.1665254948.jpg | | Frame Screws | 1 | $3.95 | $3.95 | [Zyltech](https://www.zyltech.com/100x-zyltech-m5x8-and-m5x10-button-hex-screws/) | 100x ZYLtech M5x8 Button Hex Screws: choose M5x8 (total of 74 screws needed) | <img src="https://cdn11.bigcommerce.com/s-eblil3q2nd/images/stencil/500x659/products/332/16488/Screws_Image_2__83478__71704.1665254948.jpg" width="200">
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

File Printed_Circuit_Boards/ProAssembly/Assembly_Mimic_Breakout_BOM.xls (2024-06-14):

Comment | Designator | Footprint | LCSC Part #（optional）
HDMI | J1 | HDMI-SMD | C138388
Screw Terminal | J2-3 | CONN-TH_6P-P2.54_KF128-2.54-6P | C474924
Header Pins | J4 | HDR-TH_3P-P2.54-V-M | C225478
ZH JST | J5-6 | CONN-TH-6P-P1.50_B6B-ZR_LF_SN | C157984

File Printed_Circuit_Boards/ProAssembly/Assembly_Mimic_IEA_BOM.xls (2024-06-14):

Comment | Designator | Footprint | LCSC Part #（optional）
WS2812B | U1-6 | LED-4_5050 | C114587
ZH JST | J2 | CONN-TH-6P-P1.50_B6B-ZR_LF_SN | C157984

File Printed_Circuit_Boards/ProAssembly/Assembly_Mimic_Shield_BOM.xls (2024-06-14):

Comment | Designator | Footprint | LCSC Part #（optional）
Red | D1-8 | LED_0603 | C72044
10k | R1-8 | R0603 | C103210
HDMI | J7-8 | HDMI-SMD | C138388
Connector | J1-4 | CONN-TH_P2.54_KF128-2.54-2P | C474920
Headers | J5 | HDR-TH_2P-P2.54-V-M | C492401

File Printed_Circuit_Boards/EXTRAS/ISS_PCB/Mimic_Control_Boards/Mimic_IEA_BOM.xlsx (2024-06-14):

Designator | Manufacturer Part Number or Seeed SKU | Qty | Link
WS2812B | 1528-1104-ND | 6 | https://www.digikey.com/catalog/en/partgroup/ws2812b-5050-rgb-led/51979

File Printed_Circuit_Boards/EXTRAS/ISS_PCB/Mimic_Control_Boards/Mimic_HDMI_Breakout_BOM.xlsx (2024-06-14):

Designator | Manufacturer Part Number or Seeed SKU | Qty | Link
J1 | 1747981-1 | 1 | https://www.seeedstudio.com/opl.html

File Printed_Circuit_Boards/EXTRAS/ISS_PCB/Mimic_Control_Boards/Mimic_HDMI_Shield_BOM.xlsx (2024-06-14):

Designator | Manufacturer Part Number or Seeed SKU | Qty | Link
D1,D2,D3,D4,D5,D6,D7,D8 | LTST-C191KSKT | 8 | https://www.seeedstudio.com/opl.html
R1,R2,R3,R4,R5,R6,R7,D8 | 0603WAF1002T5E | 8 | https://file.elecfans.com/web1/M00/61/0C/o4YBAFt-dwWACUP4AAh1Wgzv73Y460.pdf
J1,J2 | 1747981-1 | 2 | https://www.seeedstudio.com/opl.html

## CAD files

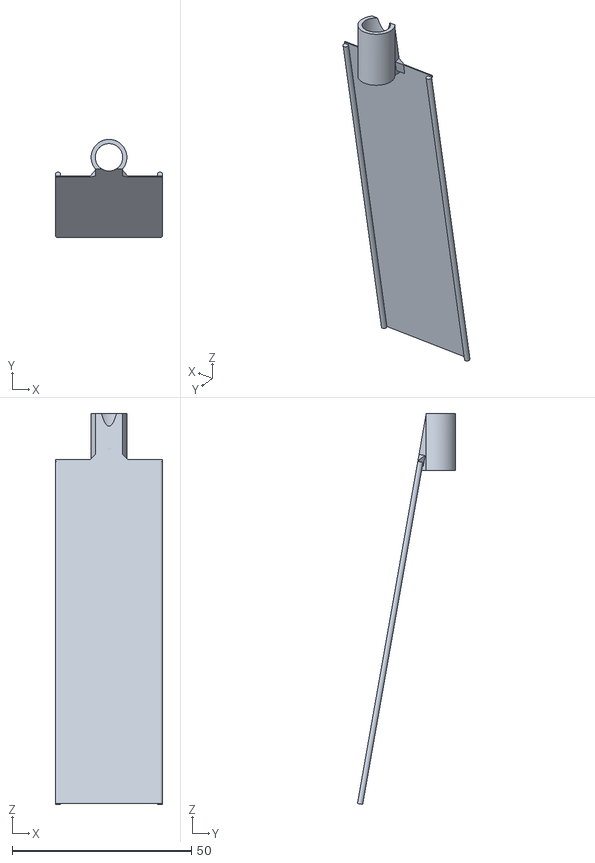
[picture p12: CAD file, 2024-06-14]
EXTRAs/Mini/3D_Printing/iROSA/0p5_Mimic_IROSA_Array_Main.stl
30.0 x 27.4 x 109.2

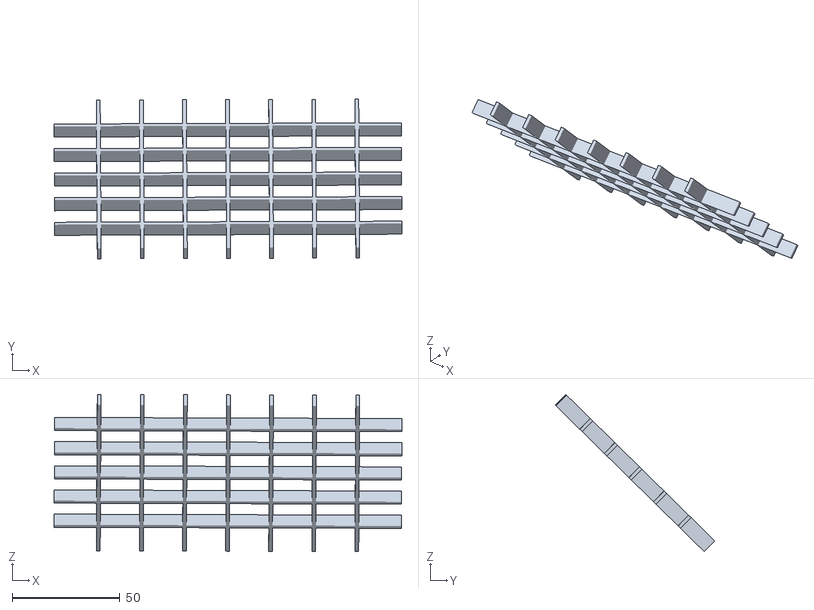
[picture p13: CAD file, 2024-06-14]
EXTRAs/SASA/Main_Ribs.stl
161.5 x 74.1 x 73.0

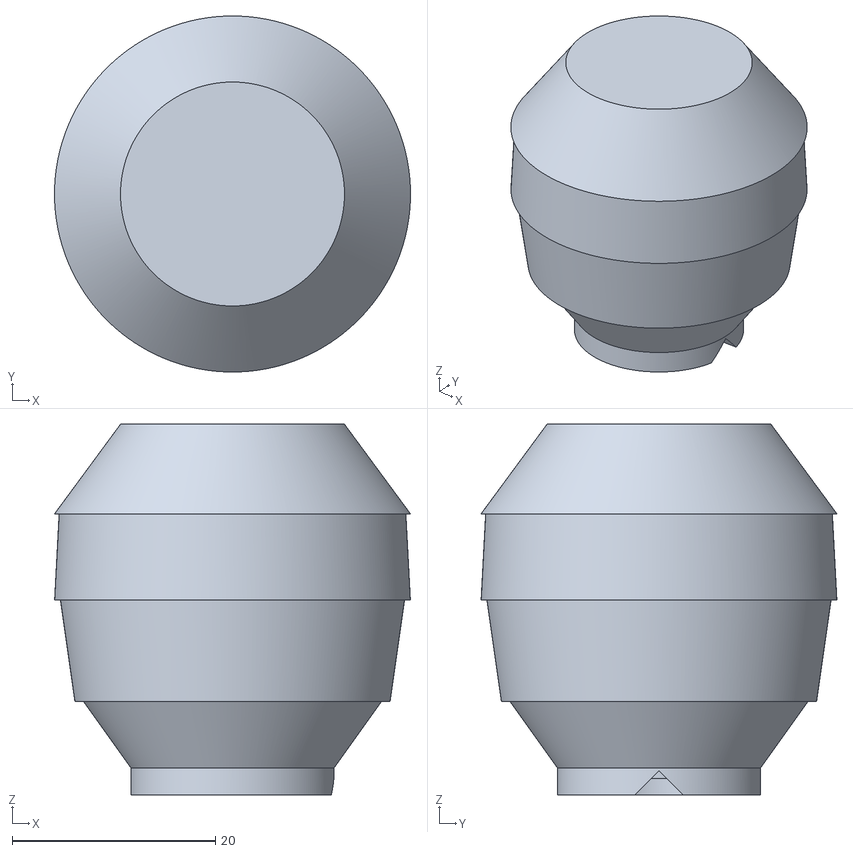
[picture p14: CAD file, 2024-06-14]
3D_Printing/BEAM/HiFi_BEAM.stl
35.0 x 35.0 x 36.5

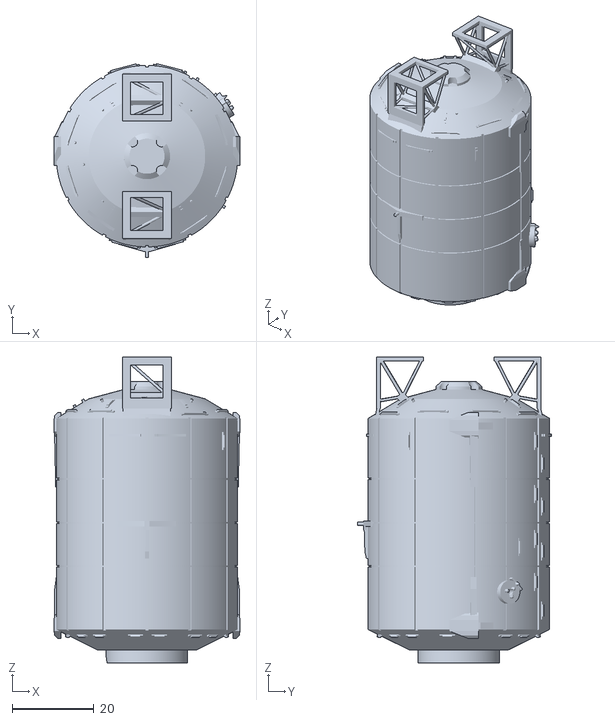
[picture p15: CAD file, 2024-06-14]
3D_Printing/Columbus/HiFi_Columbus.stl
45.6 x 47.5 x 75.0

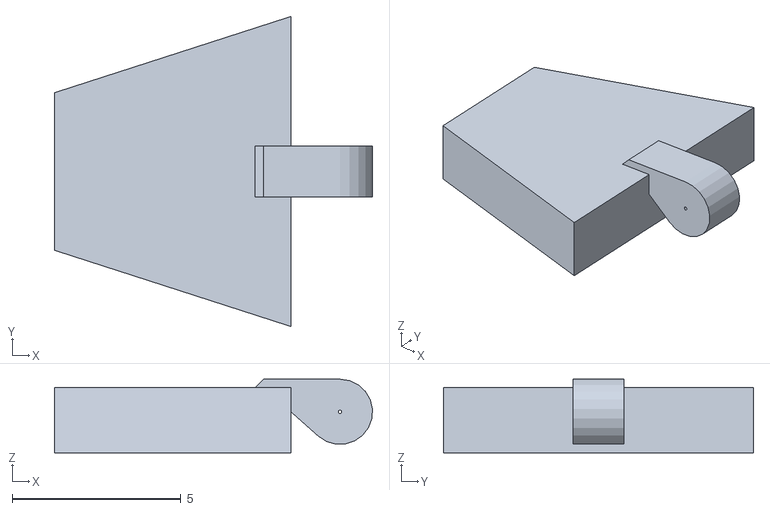
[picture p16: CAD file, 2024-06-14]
3D_Printing/Cupola/Cupola-SideWindow.stl
9.41 x 9.18 x 2.18

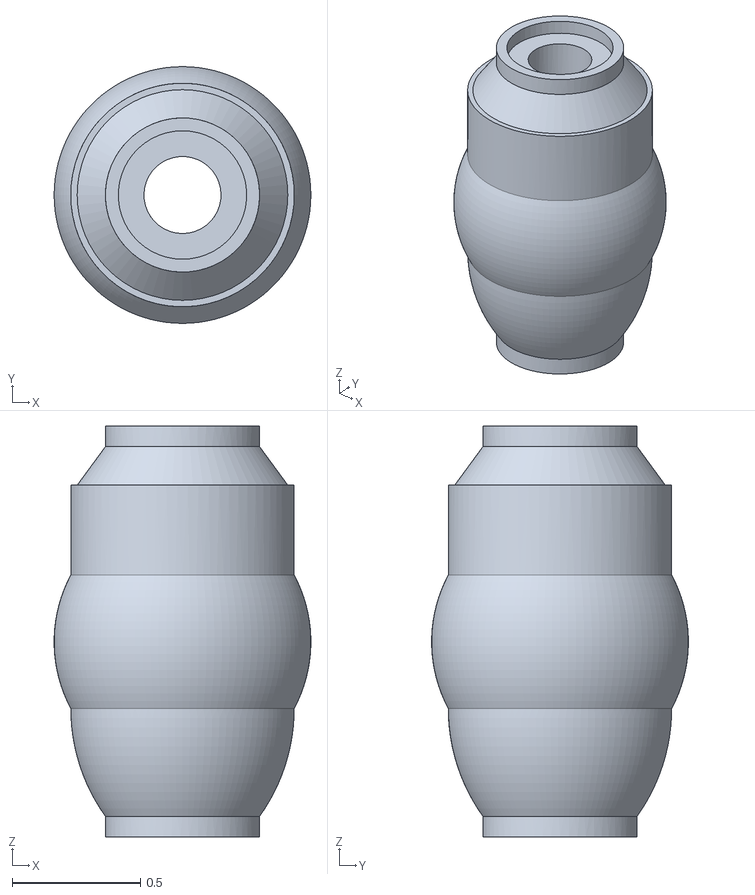
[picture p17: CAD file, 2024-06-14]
3D_Printing/DC_1_Pirs/LoFi_DockingCompartment.stl
1 x 1 x 1.60

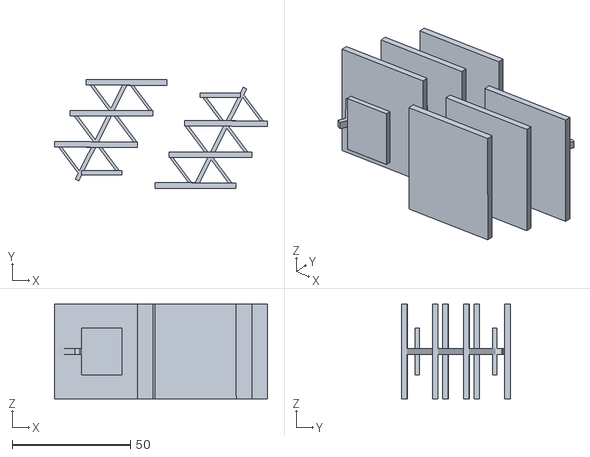
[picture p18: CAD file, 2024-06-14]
3D_Printing/FGB_Zarya/HiFi_FGB_Arrays.stl
90.1 x 46.1 x 40.0

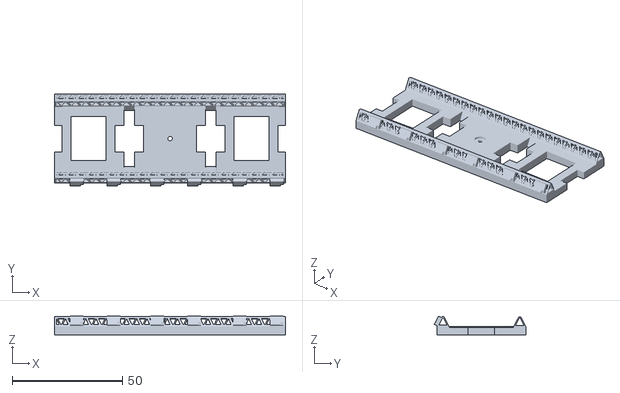
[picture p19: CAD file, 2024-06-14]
3D_Printing/HRS_Radiator_Wing/HiFi_Radiator_Beam.stl
104.7 x 41.6 x 8.51

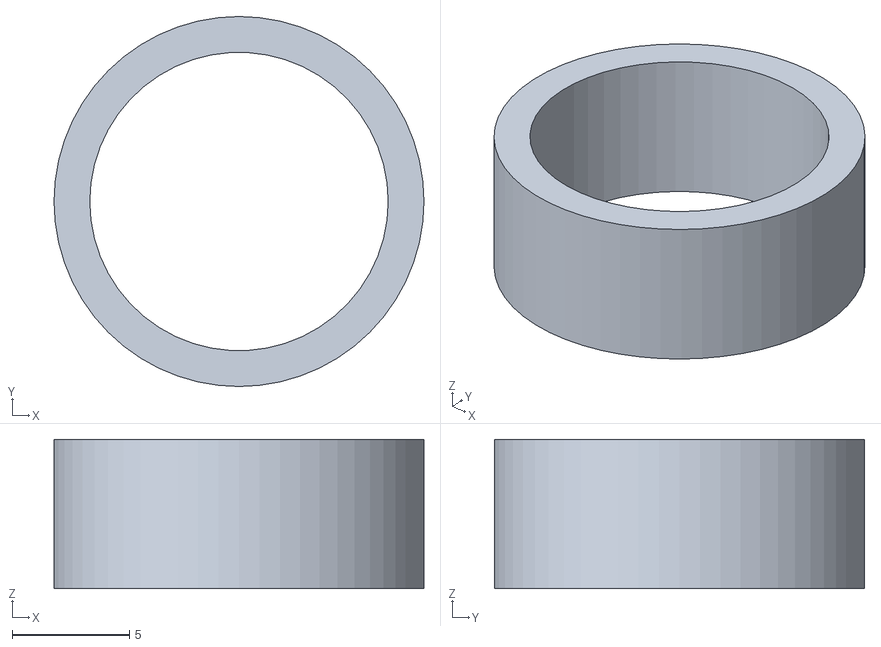
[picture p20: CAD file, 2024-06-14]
3D_Printing/IDA/LoFi_IDA23.stl
15.7 x 15.7 x 6.35

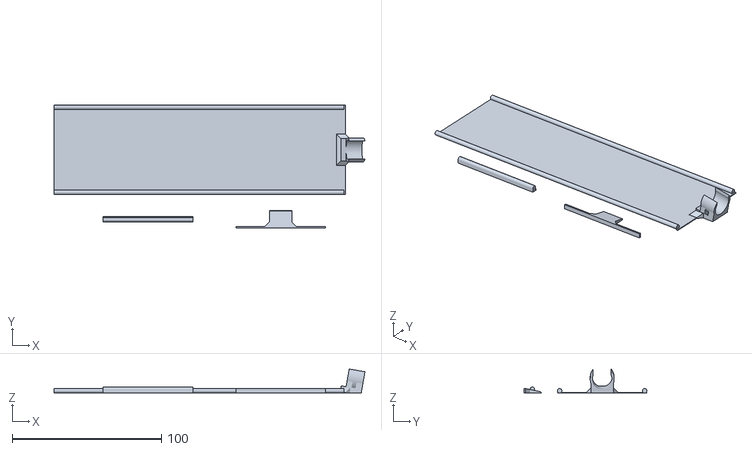
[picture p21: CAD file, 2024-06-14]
3D_Printing/IPA_Roll_Out_Solar_Arrays/HiFi_IROSA_Set.stl
208.1 x 82.3 x 16.1

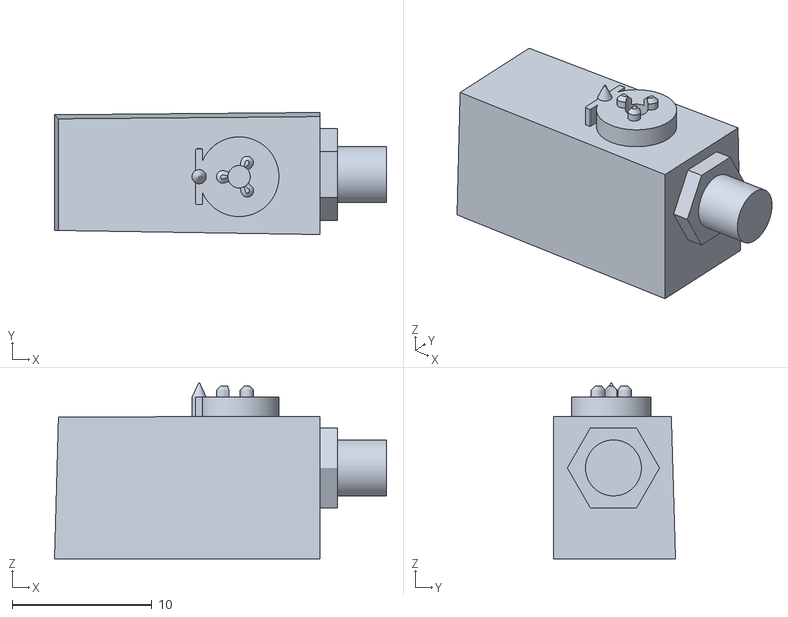
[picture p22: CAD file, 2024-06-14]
3D_Printing/JEM_EF/HiFi_JEM_EFU_Boxy.stl
23.7 x 8.73 x 12.6

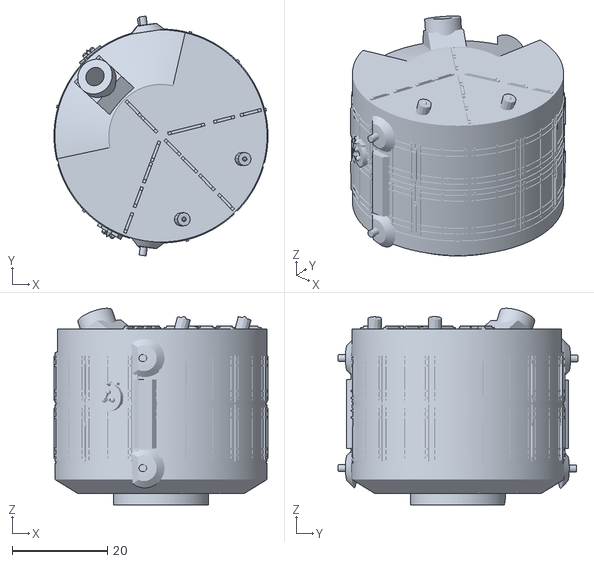
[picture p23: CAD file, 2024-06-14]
3D_Printing/JEM_ELM_PS/HiFi_JEM_JLP.stl
44.9 x 50.4 x 41.2

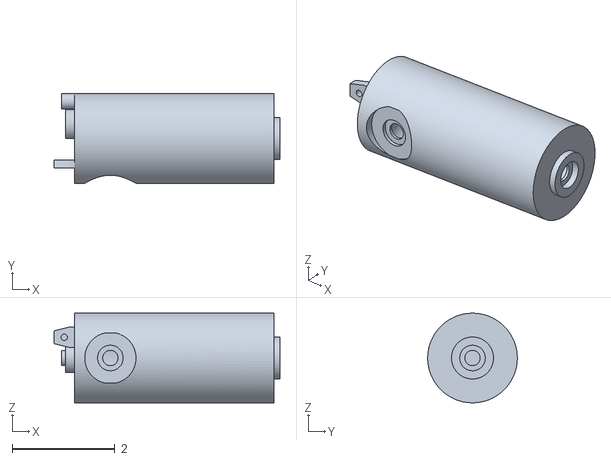
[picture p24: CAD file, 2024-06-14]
3D_Printing/JEM_Kibo/LoFi_JEM-PM-magnet_093018.stl
4.41 x 1.75 x 1.75

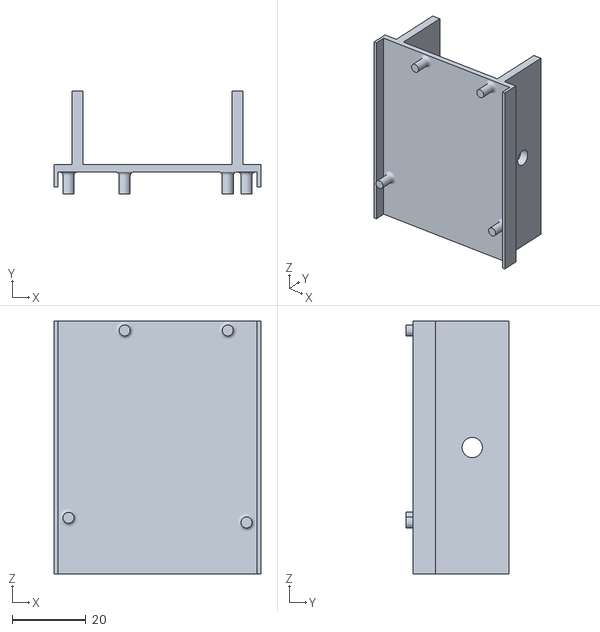
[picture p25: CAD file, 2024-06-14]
3D_Printing/Mimic_Structural_Compoments/Microcontroller_Mount_for_BGA_Controller.stl
56.0 x 28.0 x 68.6

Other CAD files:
3D_Printing/MLM_Nauka/HiFi_MLM_Radiator.stl
3D_Printing/MRM_1_Rassvet/LoFi_MRM1.stl
3D_Printing/Node_1_Unity/LoFi_UnityNode1-2.stl
3D_Printing/Node_2_Harmony/LoFi_HarmonyNode2-3_v3b.stl
3D_Printing/BEAM/HiFi_BEAM_Cap.stl
3D_Printing/BEAM/LoFi_BEAM.stl
3D_Printing/Columbus/LoFi_COF-End.stl
3D_Printing/Columbus/LoFi_LEO-COF-barrel.stl
3D_Printing/Columbus/LoFi_Leonardo_End.stl
3D_Printing/Cupola/Cupola-Body.stl
3D_Printing/Cupola/Cupola-TopWindow.stl
3D_Printing/Cupola/HiFi_Cupola.stl
3D_Printing/Cupola/HiFi_Cupola_Shutters_6x.stl
3D_Printing/FGB_Zarya/HiFi_FGB.stl
3D_Printing/FGB_Zarya/LoFi_Zarya.stl
3D_Printing/HRS_Radiator_Wing/HiFi_HRS_Radiator.stl
3D_Printing/HRS_Radiator_Wing/HiFi_HRS_Radiator_Wing.f3d
3D_Printing/HRS_Radiator_Wing/HiFi_HRS_Radiator_Wing.step
3D_Printing/HRS_Radiator_Wing/HiFi_Scissor_Beam.stl
3D_Printing/JEM_EF/HiFi_JEM_Bottom_Box_x4.stl
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

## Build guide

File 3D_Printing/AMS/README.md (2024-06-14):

# Slicer Recommendation 

|  **Sub-Assembly / Module Name** | **STL Name & Link** | **Qty** | **Filament Color** | **Slicer Comments** | **Approx Print Time [h:mm]** | **Approx Filament Used [g]** | **Approx Filament Used [m]** |
| ---- | --- | --- | --- | --- | --- | --- | --- |

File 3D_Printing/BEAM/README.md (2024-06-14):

# Slicer Recommendation 

|  **Sub-Assembly / Module Name** | **STL Name & Link** | **Qty** | **Filament Color** | **Slicer Comments** | **Approx Print Time [h:mm]** | **Approx Filament Used [g]** | **Approx Filament Used [m]** |
| ---- | --- | --- | --- | --- | --- | --- | --- |
| BEAM | [LoFi_BEAM](https://github.com/ISS-Mimic/Mimic/blob/main/3D_Printing/BEAM/LoFi_BEAM.stl) | 1 | white | 0.16mm; 10%; supports | 1:07 | 13 | 4.22 |


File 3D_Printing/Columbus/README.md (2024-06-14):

# Slicer Recommendation 

|  **Sub-Assembly / Module Name** | **STL Name & Link** | **Qty** | **Filament Color** | **Slicer Comments** | **Approx Print Time [h:mm]** | **Approx Filament Used [g]** | **Approx Filament Used [m]** |
| ---- | --- | --- | --- | --- | --- | --- | --- |
| COF / Columbus | [LoFi_LEO-COF-barrel](https://github.com/ISS-Mimic/Mimic/blob/main/3D_Printing/Columbus/LoFi_LEO-COF-barrel.stl) | 1 | Silver | 0.16mm; 10%; supports | 6:09 | 45 | 14.95 |
|  | [LoFi_COF-End](https://github.com/ISS-Mimic/Mimic/blob/main/3D_Printing/Columbus/LoFi_COF-End.stl) | 1 | Silver | 0.16mm; 10%; supports | - | - | - |


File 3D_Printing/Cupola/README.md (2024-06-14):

# Slicer Recommendation 

|  **Sub-Assembly / Module Name** | **STL Name & Link** | **Qty** | **Filament Color** | **Slicer Comments** | **Approx Print Time [h:mm]** | **Approx Filament Used [g]** | **Approx Filament Used [m]** |
| ---- | --- | --- | --- | --- | --- | --- | --- |
| Cupola | [Cupola-Body](https://github.com/ISS-Mimic/Mimic/blob/main/3D_Printing/Cupola/Cupola-Body.stl) | 1 | Silver | 0.12mm;10%;supports; raft | 1:17 | 8 | 2.54 |
| Cupola | [Cupola-Sidewindow](https://github.com/ISS-Mimic/Mimic/blob/main/3D_Printing/Cupola/Cupola-SideWindow.stl) | 6 | Silver | 0.12mm; 10%;supports; raft | - | - | - |
| Cupola | [Cupola-TopWindow](https://github.com/ISS-Mimic/Mimic/blob/main/3D_Printing/Cupola/Cupola-TopWindow.stl) | 1 | Silver | 0.12mm; 10%;supports; raft | - | - | - |


Note : Jewlers hand drill is needed for assembly

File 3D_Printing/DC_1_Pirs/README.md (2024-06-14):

*THIS MODULE IS NO LONGER PART OF ISS CURRENT ASSEMBLY*

# Slicer Recommendation 

|  **Sub-Assembly / Module Name** | **STL Name & Link** | **Qty** | **Filament Color** | **Slicer Comments** | **Approx Print Time [h:mm]** | **Approx Filament Used [g]** | **Approx Filament Used [m]** |
| ---- | --- | --- | --- | --- | --- | --- | --- |
| Docking Compartment | [LoFi_DockingCompartment.stl](https://github.com/ISS-Mimic/Mimic/blob/main/3D_Printing/DC_1_Pirs/LoFi_DockingCompartment.stl) | 1 | Vanallia White | 0.12mm;10%;supports | 1:31 | 8.4 | 2.8 |



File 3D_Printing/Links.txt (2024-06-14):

https://github.com/ISS-Mimic/Mimic/blob/main/3D_Printing/IDA/LoFi_IDA23.stl
https://github.com/ISS-Mimic/Mimic/blob/main/3D_Printing/BEAM/LoFi_BEAM.stl
https://github.com/ISS-Mimic/Mimic/blob/main/3D_Printing/Truss_S6/LoFi_ITS-6_LS-complex.stl
https://github.com/ISS-Mimic/Mimic/blob/main/3D_Printing/Truss_S6/HiFi_Truss_S6.stl
https://github.com/ISS-Mimic/Mimic/blob/main/3D_Printing/Truss_S6/LoFi_ITS-6-simple.stl
https://github.com/ISS-Mimic/Mimic/blob/main/3D_Printing/Truss_S6/LoFi_ITS-6_IEA-complex.stl
https://github.com/ISS-Mimic/Mimic/blob/main/3D_Printing/Truss_P3/LoFi_ITS-P3-complex.stl
https://github.com/ISS-Mimic/Mimic/blob/main/3D_Printing/MRM_1_Rassvet/LoFi_MRM1.stl
https://github.com/ISS-Mimic/Mimic/blob/main/3D_Printing/US_Lab_Destiny/LoFi_DestinyLab-1.stl
https://github.com/ISS-Mimic/Mimic/blob/main/3D_Printing/US_Lab_Destiny/LoFi_DestinyLab-2.stl
https://github.com/ISS-Mimic/Mimic/blob/main/3D_Printing/Columbus/LoFi_COF-End.stl
https://github.com/ISS-Mimic/Mimic/blob/main/3D_Printing/Columbus/LoFi_LEO-COF-barrel.stl
https://github.com/ISS-Mimic/Mimic/blob/main/3D_Printing/Columbus/LoFi_Leonardo_End.stl
https://github.com/ISS-Mimic/Mimic/blob/main/3D_Printing/FGB_Zarya/LoFi_Zarya.stl
https://github.com/ISS-Mimic/Mimic/blob/main/3D_Printing/DC_1_Pirs/LoFi_DockingCompartment.stl
https://github.com/ISS-Mimic/Mimic/blob/main/3D_Printing/Truss_S1/LoFi_ITS-1.stl
https://github.com/ISS-Mimic/Mimic/blob/main/3D_Printing/Truss_S1/LoFi_ITS-1_TRRJ-Beam.stl
https://github.com/ISS-Mimic/Mimic/blob/main/3D_Printing/Truss_S1/LoFi_S1_093018.stl
https://github.com/ISS-Mimic/Mimic/blob/main/3D_Printing/Truss_S1/LoFi_ITS-1_Mounts.stl
https://github.com/ISS-Mimic/Mimic/blob/main/3D_Printing/Truss_S1/LoFi_ITS-1_AmmoniaTank.stl
https://github.com/ISS-Mimic/Mimic/blob/main/3D_Printing/Truss_S3/LoFi_ITS-3-simple.stl
https://github.com/ISS-Mimic/Mimic/blob/main/3D_Printing/Truss_S3/LoFi_ITS-S3-complex.stl
https://github.com/ISS-Mimic/Mimic/blob/main/3D_Printing/Truss_S3/LoFi_ITS-3_SARJ_Gear_Ring.stl
https://github.com/ISS-Mimic/Mimic/blob/main/3D_Printing/Node_2_Harmony/LoFi_HarmonyNode2-2.stl
https://github.com/ISS-Mimic/Mimic/blob/main/3D_Printing/Node_2_Harmony/LoFi_HarmonyNode2-3_v3b.stl
https://github.com/ISS-Mimic/Mimic/blob/main/3D_Printing/Node_2_Harmony/LoFi_HarmonyNode2-3_v3a.stl
https://github.com/ISS-Mimic/Mimic/blob/main/3D_Printing/Node_2_Harmony/LoFi_node2-3-magnet-endcap_093018.stl
https://github.com/ISS-Mimic/Mimic/blob/main/3D_Printing/Node_2_Harmony/LoFi_node2-3-magnet-barrel_093018.stl
https://github.com/ISS-Mimic/Mimic/blob/main/3D_Printing/Node_2_Harmony/LoFi_HarmonyNode2-1.stl
https://github.com/ISS-Mimic/Mimic/blob/main/3D_Printing/US_Airlock_Quest/HiFi_QuestAirlock2.stl
https://github.com/ISS-Mimic/Mimic/blob/main/3D_Printing/US_Airlock_Quest/HiFi_QuestTank.stl
https://github.com/ISS-Mimic/Mimic/blob/main/3D_Printing/US_Airlock_Quest/HiFi_QuestToolbox.stl
https://github.com/ISS-Mimic/Mimic/blob/main/3D_Printing/US_Airlock_Quest/HiFi_QuestToolboxMnt.stl
https://github.com/ISS-Mimic/Mimic/blob/main/3D_Printing/US_Airlock_Quest/HiFi_QuestAirlock1.stl
https://github.com/ISS-Mimic/Mimic/blob/main/3D_Printing/JEM_Kibo/LoFi_JEM-PM.stl
https://github.com/ISS-Mimic/Mimic/blob/main/3D_Printing/JEM_Kibo/LoFi_JEM-PM-magnet_093018.stl
https://github.com/ISS-Mimic/Mimic/blob/main/3D_Printing/JEM_ELM_PS/LoFi_JEM-ELM-magnet_093018.stl
https://github.com/ISS-Mimic/Mimic/blob/main/3D_Printing/JEM_ELM_PS/LoFi_JEM-PS.stl
https://github.com/ISS-Mimic/Mimic/blob/main/3D_Printing/SSRMS_Canadarm_and_MT_MBS/LoFi_Canadaarm2_EE.stl
https://github.com/ISS-Mimic/Mimic/blob/main/3D_Printing/SSRMS_Canadarm_and_MT_MBS/LoFi_MobileBaseSystem_Base.stl
https://github.com/ISS-Mimic/Mimic/blob/main/3D_Printing/SSRMS_Canadarm_and_MT_MBS/LoFi_Canadaarm2_Arm.stl
https://github.com/ISS-Mimic/Mimic/blob/main/3D_Printing/SSRMS_Canadarm_and_MT_MBS/LoFi_MobileBaseSystem_Body.stl
https://github.com/ISS-Mimic/Mimic/blob/main/3D_Printing/Truss_P1/LoFi_ITS-P1andS1.stl
https://github.com/ISS-Mimic/Mimic/blob/main/3D_Printing/Truss_P6/HiFi_Truss_P6_TTCR.stl
https://github.com/ISS-Mimic/Mimic/blob/main/3D_Printing/Truss_P6/HiFi_Truss_P6_PFCS.stl
https://github.com/ISS-Mimic/Mimic/blob/main/3D_Printing/Truss_P6/HiFi_Truss_P6.stl
https://github.com/ISS-Mimic/Mimic/blob/main/3D_Printing/Truss_P6/HiFi_Truss_P6_STCR.stl
https://github.com/ISS-Mimic/Mimic/blob/main/3D_Printing/EVA_Astronaut/EMU.stl
https://github.com/ISS-Mimic/Mimic/blob/main/3D_Printing/Visiting_Vehicles/Progress/HiFi_Progress.stl
https://github.com/ISS-Mimic/Mimic/blob/main/3D_Printing/Visiting_Vehicles/Cygnus/CygnusEnhanced.stl
https://github.com/ISS-Mimic/Mimic/blob/main/3D_Printing/Visiting_Vehicles/Soyuz/HiFi_Soyuz_Antenna.stl
https://github.com/ISS-Mimic/Mimic/blob/main/3D_Printing/Visiting_Vehicles/Soyuz/HiFi_Soyuz_Final.stl
https://github.com/ISS-Mimic/Mimic/blob/main/3D_Printing/PV_Radiator/HiFi_PVR_ScissorBeam_1x.stl
https://github.com/ISS-Mimic/Mimic/blob/main/3D_Printing/PV_Radiator/HiFi_PVR_P4.stl
https://github.com/ISS-Mimic/Mimic/blob/main/3D_Printing/PV_Radiator/HiFi_PVR.stl
https://github.com/ISS-Mimic/Mimic/blob/main/3D_Printing/Truss_S4_S5_P4_P5/LoFi_ITS-4_SARJ_Connector.stl
https://github.com/ISS-Mimic/Mimic/blob/main/3D_Printing/Truss_S4_S5_P4_P5/HiFi_Truss_PS45.stl
https://github.com/ISS-Mimic/Mimic/blob/main/3D_Printing/Truss_S4_S5_P4_P5/LoFi_ITS-4_5-simple.stl
https://github.com/ISS-Mimic/Mimic/blob/main/3D_Printing/Truss_S4_S5_P4_P5/LoFi_ITS-4_5-complex.stl
https://github.com/ISS-Mimic/Mimic/blob/main/3D_Printing/Truss_S4_S5_P4_P5/LoFi_OutboardRadiatorBase.stl
https://github.com/ISS-Mimic/Mimic/blob/main/3D_Printing/Node_1_Unity/LoFi_UnityNode1-2.stl
https://github.com/ISS-Mimic/Mimic/blob/main/3D_Printing/Node_1_Unity/LoFi_UnityNode1-1.stl
https://github.com/ISS-Mimic/Mimic/blob/main/3D_Printing/Node_1_Unity/LoFi_UnityNode1-v2a.stl
https://github.com/ISS-Mimic/Mimic/blob/main/3D_Printing/Node_1_Unity/LoFi_UnityNode1-v2b.stl
https://github.com/ISS-Mimic/Mimic/blob/main/3D_Printing/PMA/LoFi_PMA123.stl
https://github.com/ISS-Mimic/Mimic/blob/main/3D_Printing/PMA/HiFi_PMA2.stl
https://github.com/ISS-Mimic/Mimic/blob/main/3D_Printing/Mimic_Structural_Compoments/Metro 2040 Mount.stl
https://github.com/ISS-Mimic/Mimic/blob/main/3D_Printing/Mimic_Structural_Compoments/Sabrent USB Hub Mount.stl
https://github.com/ISS-Mimic/Mimic/blob/main/3D_Printing/Mimic_Structural_Compoments/LoFi_Outboard-Truss-support.stl
https://github.com/ISS-Mimic/Mimic/blob/main/3D_Printing/Mimic_Structural_Compoments/Outboard_Truss_Interface.stl
https://github.com/ISS-Mimic/Mimic/blob/main/3D_Printing/Mimic_Structural_Compoments/HDMI-PCB-Holder.stl
https://github.com/ISS-Mimic/Mimic/blob/main/3D_Printing/Mimic_Structural_Compoments/LoFi_2020-endcap-tall.stl
https://github.com/ISS-Mimic/Mimic/blob/main/3D_Printing/Cupola/Cupola-Body.stl
https://github.com/ISS-Mimic/Mimic/blob/main/3D_Printing/Cupola/Cupola-SideWindow.stl
https://github.com/ISS-Mimic/Mimic/blob/main/3D_Printing/Cupola/Cupola-TopWindow.stl
https://github.com/ISS-Mimic/Mimic/blob/main/3D_Printing/SM_Zvezda/LoFi_ServiceModule-ant-boom.stl
https://github.com/ISS-Mimic/Mimic/blob/main/3D_Printing/SM_Zvezda/LoFi_Zvezda.stl
https://github.com/ISS-Mimic/Mimic/blob/main/3D_Printing/SM_Zvezda/LoFi_ServiceModule-ant-dish.stl
https://github.com/ISS-Mimic/Mimic/blob/main/3D_Printing/SM_Zvezda/LoFi_Zvezda_End.stl
https://github.com/ISS-Mimic/Mimic/blob/main/3D_Printing/Truss_Z1/MidFi_Truss_Z1.stl
https://github.com/ISS-Mimic/Mimic/blob/main/3D_Printing/Truss_Z1/HiFi_Truss_Z1_Scuff_Plate.stl
https://github.com/ISS-Mimic/Mimic/blob/main/3D_Printing/Truss_Z1/HiFi_Truss_Z1_Top.stl
https://github.com/ISS-Mimic/Mimic/blob/main/3D_Printing/Truss_Z1/LoFi-ITS-Z1.stl
https://github.com/ISS-Mimic/Mimic/blob/main/3D_Printing/Truss_Z1/HiFi_Truss_Z1_Bottom.stl
https://github.com/ISS-Mimic/Mimic/blob/main/3D_Printing/Truss_Z1/HiFi_Truss_Z1_SASA.stl
https://github.com/ISS-Mimic/Mimic/blob/main/3D_Printing/Truss_Z1/HiFi_Truss_Z1_Tray.stl
https://github.com/ISS-Mimic/Mimic/blob/main/3D_Printing/Truss_Z1/HiFi_Truss_Z1_CMG_Plate.stl
https://github.com/ISS-Mimic/Mimic/blob/main/3D_Printing/Solar_Array_Wing/HiFi_Solar_Array_Wing.stl
https://github.com/ISS-Mimic/Mimic/blob/main/3D_Printing/Solar_Array_Wing/LoFi_Solar_Array_Wing.stl
https://github.com/ISS-Mimic/Mimic/blob/main/3D_Printing/JEM_EF/HiFi_JEM_EF.stl
https://github.com/ISS-Mimic/Mimic/blob/main/3D_Printing/MLM_Nauka/LoFi-MLM-Airlock.stl
https://github.com/ISS-Mimic/Mimic/blob/main/3D_Printing/MLM_Nauka/LoFi-MLM-Airlock-Hatch.stl
https://github.com/ISS-Mimic/Mimic/blob/main/3D_Printing/Truss_S0/LoFi_ITS-S0.stl
https://github.com/ISS-Mimic/Mimic/blob/main/3D_Printing/Truss_S0/LoFi_ITS-S0-Destiny_Connector.stl
https://github.com/ISS-Mimic/Mimic/blob/main/3D_Printing/Truss_S0/LoFi_S0-093018.stl
https://github.com/ISS-Mimic/Mimic/blob/main/3D_Printing/HRS_Radiator_Wing/HiFi_Radiator_Beam.stl
https://github.com/ISS-Mimic/Mimic/blob/main/3D_Printing/HRS_Radiator_Wing/HiFi_Scissor_Beam.stl
https://github.com/ISS-Mimic/Mimic/blob/main/3D_Printing/HRS_Radiator_Wing/HiFi_HRS_Radiator.stl

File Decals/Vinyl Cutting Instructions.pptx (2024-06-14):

## Vinyl Cutting

ISS solar cells

Chen Deng
Raindrop8888@gmail.com
440-382-3839 (cell)

## Goal

Quantity needed: 24 panels. 5 panels per sheet, therefore need 5 cuts
Size setting: 32 cm x 4.5 cm

32 cm

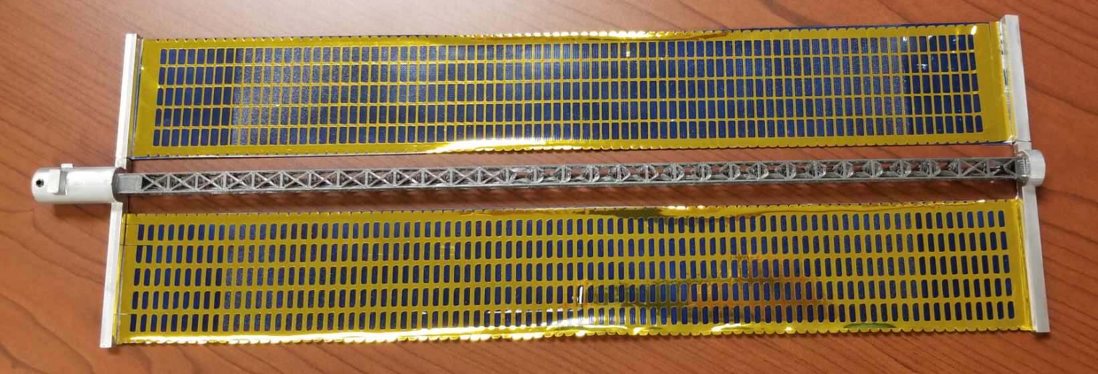
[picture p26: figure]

4.5 cm

## File -> import

(If import image doesn't have the nice lacy edges, see lessons learned page below)

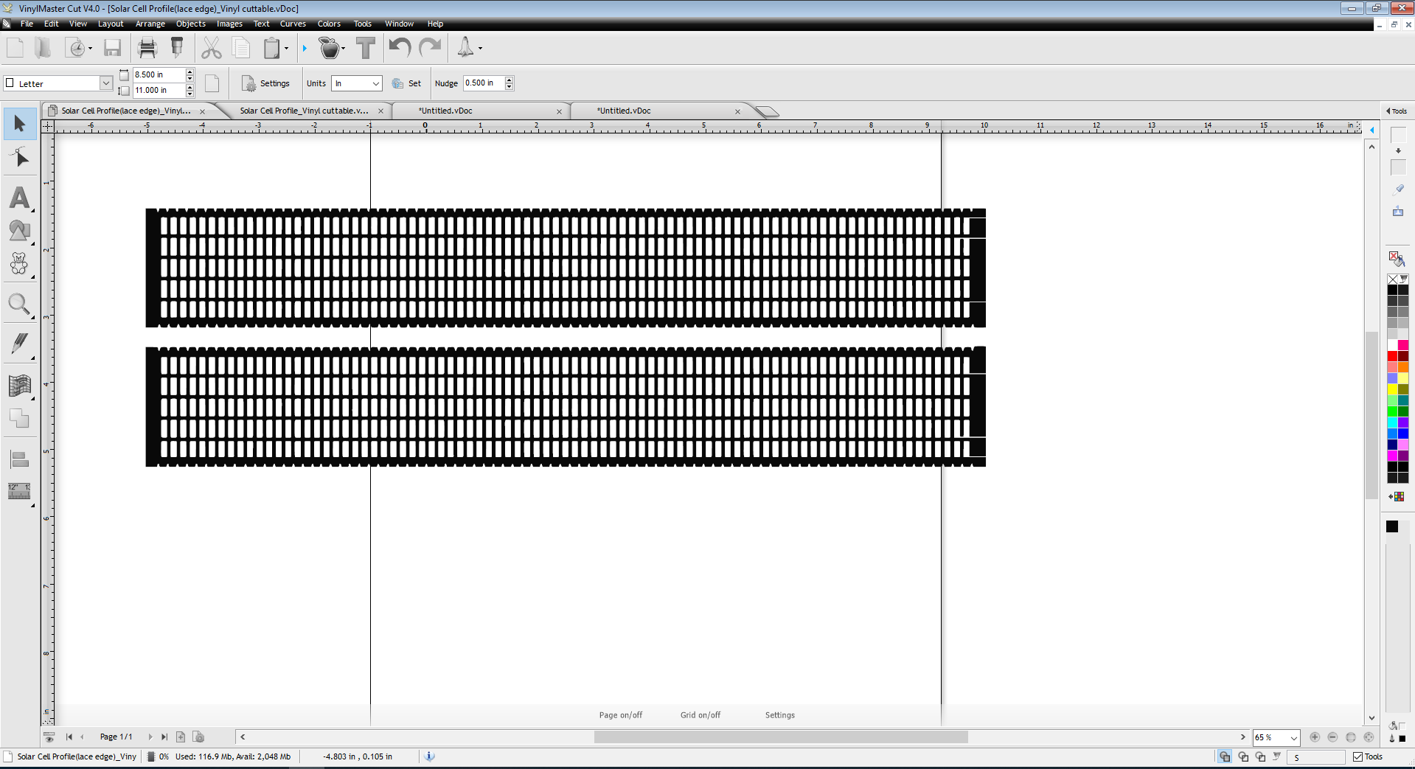
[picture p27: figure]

## Cut icon

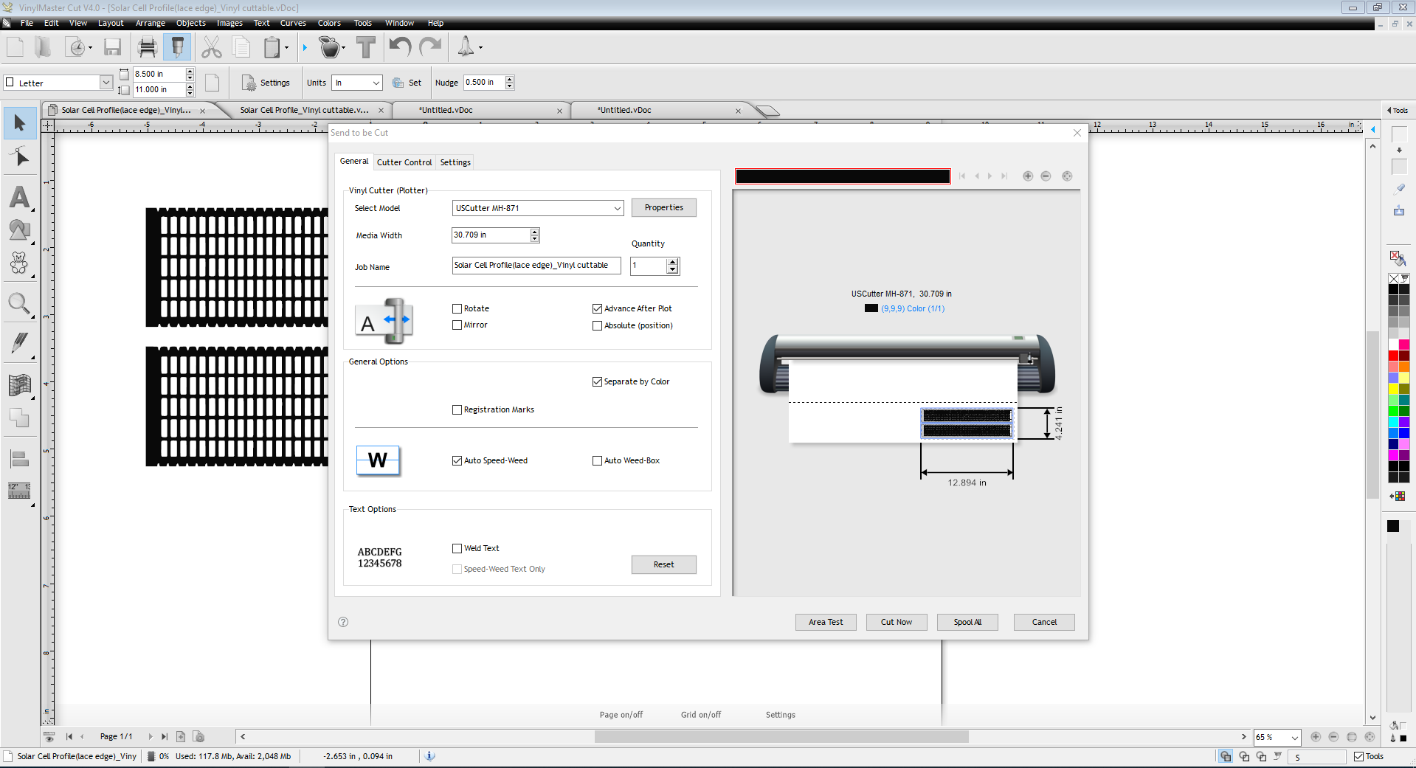
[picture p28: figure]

## Area Test (This will allow cutter to show the area to be cut, to make sure vinyl is in the correct area)

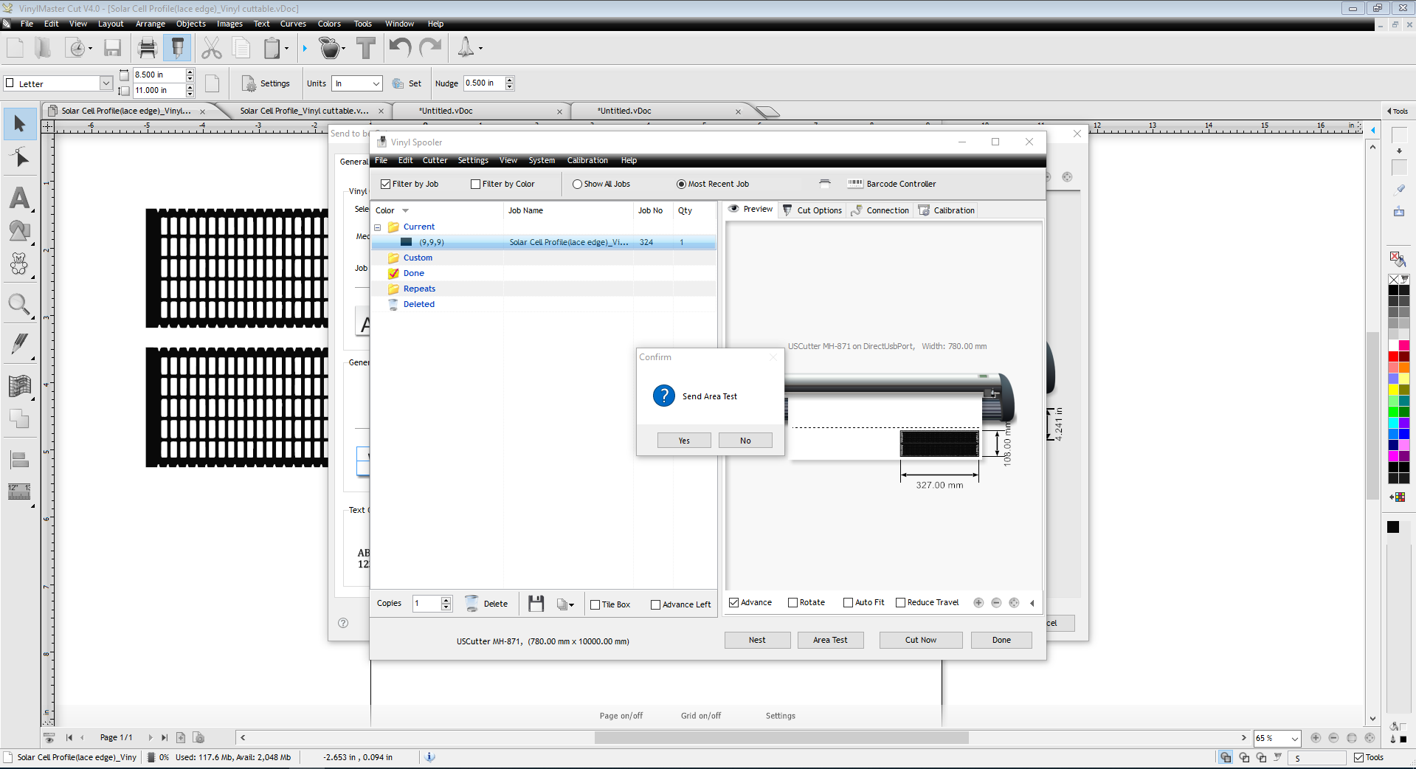
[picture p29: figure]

## Cut confirmation

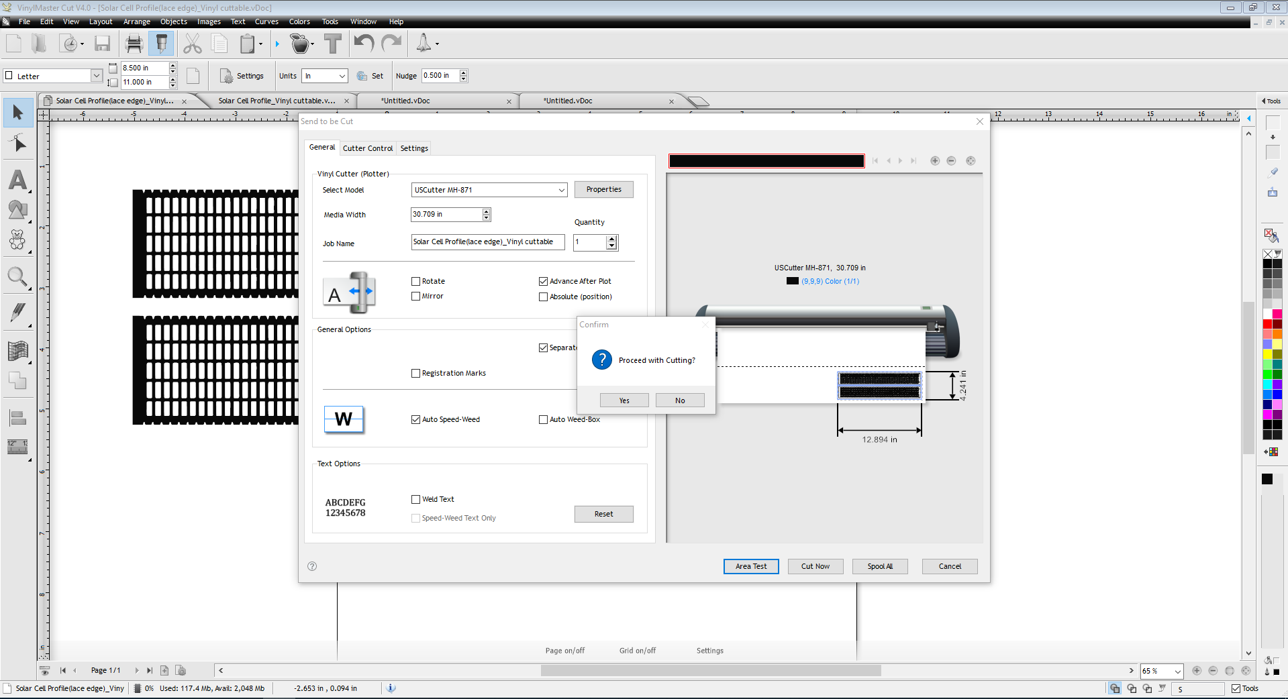
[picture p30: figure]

## Cut Now – Command to cut Vinyl

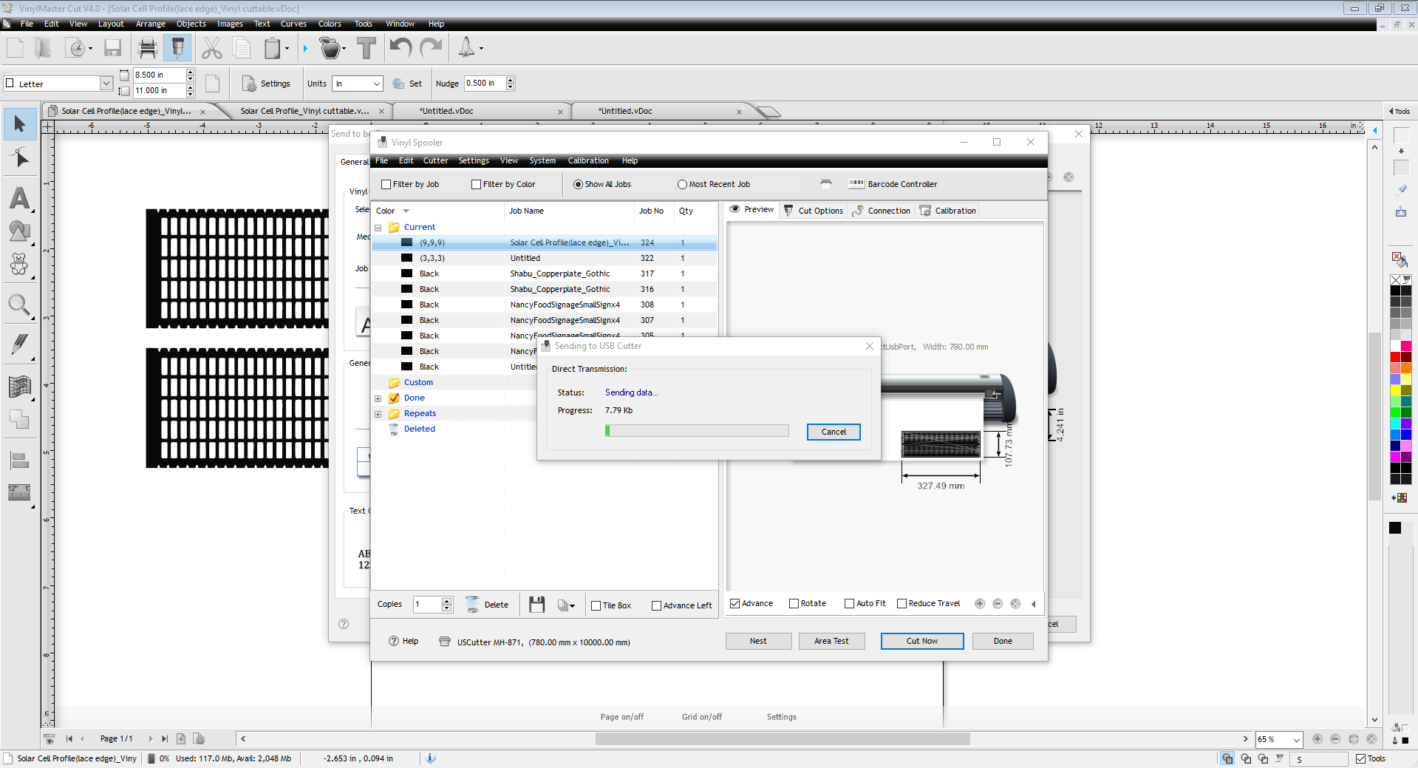
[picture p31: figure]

## Lessons Learned: Issue(s) encountered

Issue 1: SVG file did not import properly. Aka, image was did not display correctly, no lacy edges
Work around: Imported SVG to Inkscape, then export to PNG. This make a screen shot of image. Then import PNG file to VinylMast Cut V4.0
Issue 2: VinylMaster Cut V4.0 gave error (Nothing to cut)
Work around: While in VinylMaster program:
- Click “Vectorizer”
- Click “trace”
http (http://forum.uscutter.com/index.php?/topic/53598-vinylmaster-cut-trace-issue/)://forum.uscutter.com/index.php?/topic/53598-vinylmaster-cut-trace-issue/

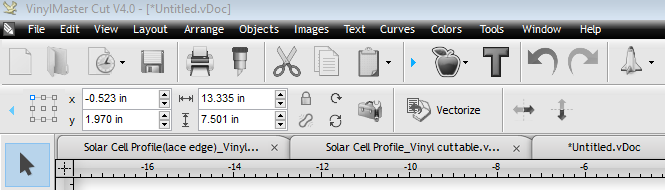
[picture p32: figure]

## What file type need for Vinyl cutting at Freeman Branch Library

- Program to used for cutting is VinylMaster Cut V4.0, which has extension of .vDoc
- Files type can be imported:
  - SVG file
  - Adobe Illustrator file
  - PNG file

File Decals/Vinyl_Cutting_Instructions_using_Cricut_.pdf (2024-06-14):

# Cutting SAW Vinyl with Cricut Maker

### Last updated: 2021.05.04 May the 4th be with you!

# What you are making

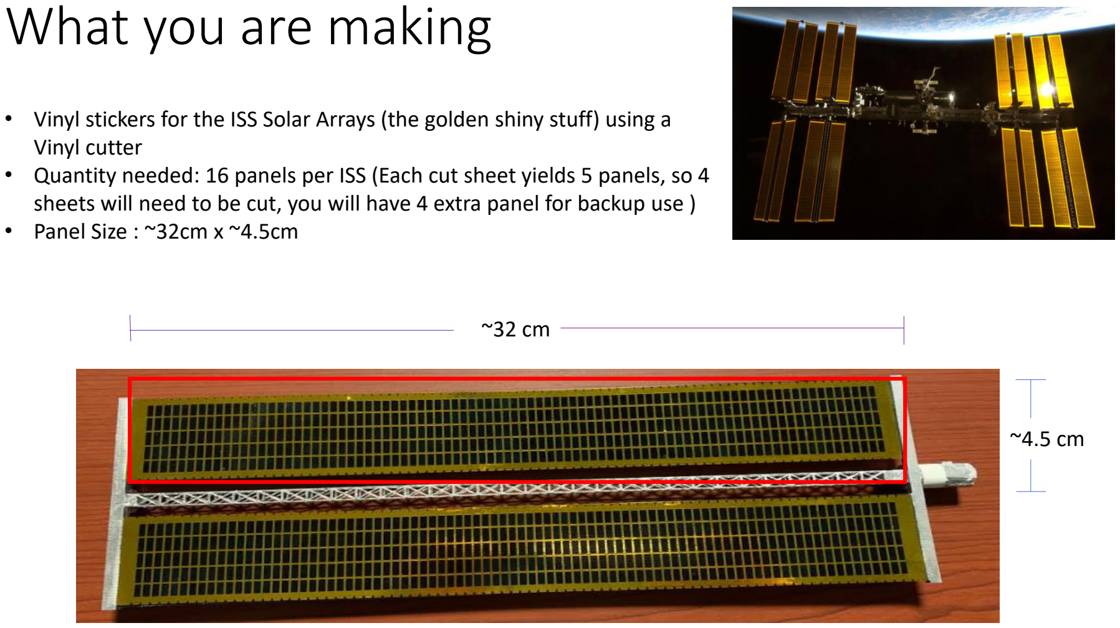
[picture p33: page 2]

- Vinyl stickers for the ISS Solar Arrays (the golden shiny stuff) using a Vinyl cutter
- Quantity needed: 16 panels per ISS (Each cut sheet yields 5 panels, so 4 sheets will need to be cut, you will have 4 extra panel for backup use )
- Panel Size : ~32cm x ~4.5cm

~32 cm

~4.5 cm

# Here is what you need

## - Cricut Maker (https://cricut.com/en_us/machines/cricut-maker.html) - Cricut Design Space (https://design.cricut.com/) v6.7.201 (used here for images)

- SAW file (https://raw.githubusercontent.com/ISS-Mimic/Mimic/master/Decals/SAW_svg_working.svg) (download from Github)

## - 3D printed & painted ISS Solar Array

- 12” x 24” Cricut mat (https://www.joann.com/cricut-cutting-mat-12inx24in-2/pkg-standardgrip/9287830.html)

## - Shiny Vinyl (https://www.amazon.com/gp/product/B07XZ3XY42/) - Transfer tape (https://www.amazon.com/Cricut-2002363-Vinyl-Transfer-Tape/dp/B00LJV1KYO)

- Embossing tool (https://www.michaels.com/embossing-stylus-tool-set-by-craft-smart/10045694.html?r=g&Kenshoo_ida=) or Weeding tool (https://www.amazon.com/Cricut-2004233-Tools-Weeding-Kit/dp/B071KMBGCR?hvadid=198059709086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)

## - Tweezers (optional, but recommended) - Scissors or Paper cutter - Patience + loads of time for weeding

1) Turn on & plug in Cricut Maker
2) On computer, launch Cricut Design Space
3) Click New Project
- Project image will be saved to My Projects for future use after initial upload (see example right)
4) Click Upload
5) Click Upload Image
6) Drag and drop ISS SAW file into window or click Browse to locate file to upload
7) Click Upload
8) Click the image/project you just uploaded under Recent Uploads
9) Click Insert Images, then image will show up on the canvas

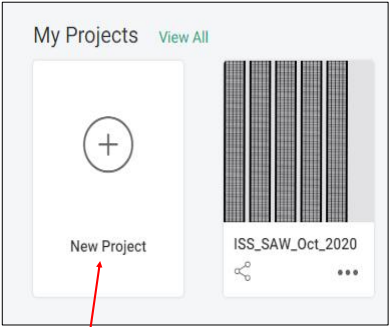
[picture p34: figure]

3

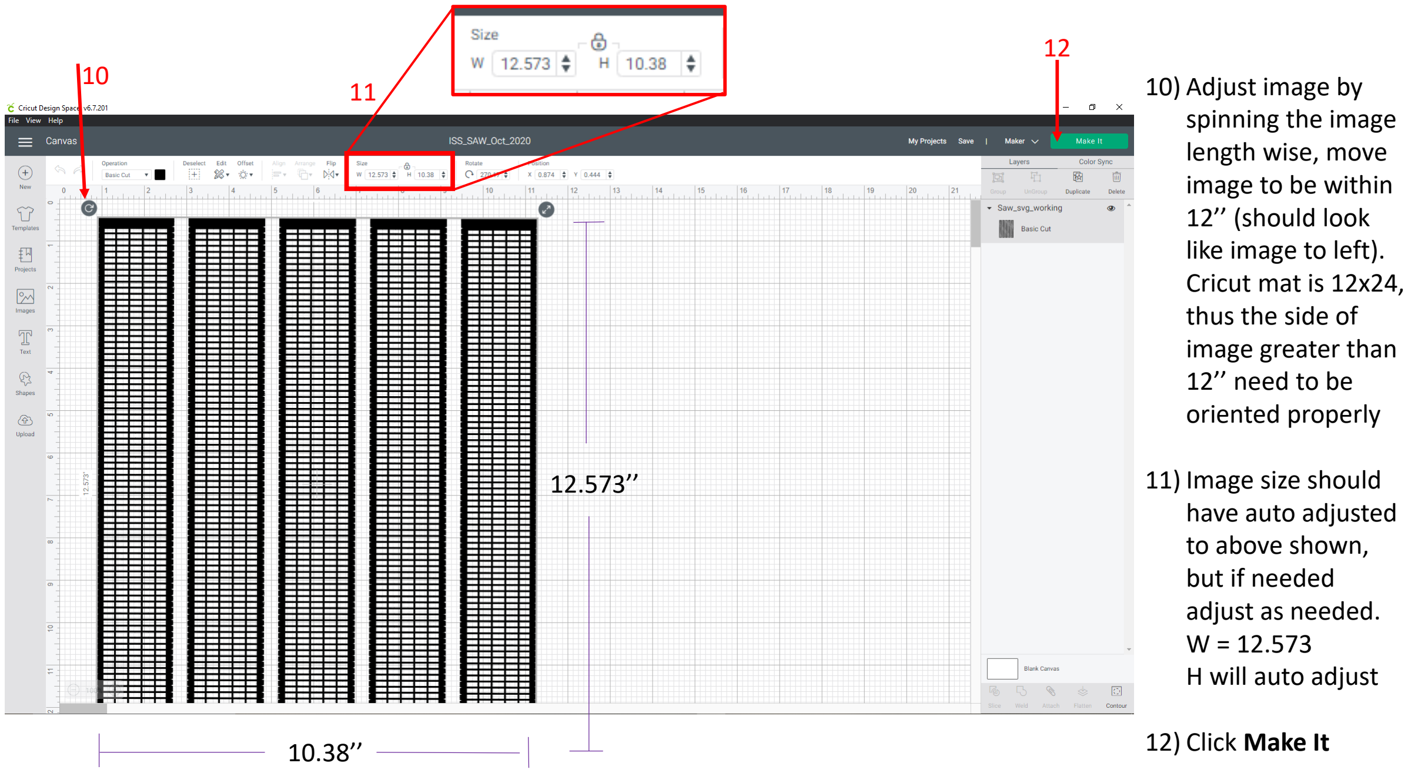
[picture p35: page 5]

10) Adjust image by
spinning the image
length wise, move
image to be within
12’’ (should look
like image to left).
Cricut mat is 12x24,
thus the side of
image greater than
12’’ need to be
oriented properly
11) Image size should
have auto adjusted
to above shown,
but if needed
adjust as needed.
W = 12.573
H will auto adjust
12) Click Make It

12.573’’

10.38’’

12
10 | 11

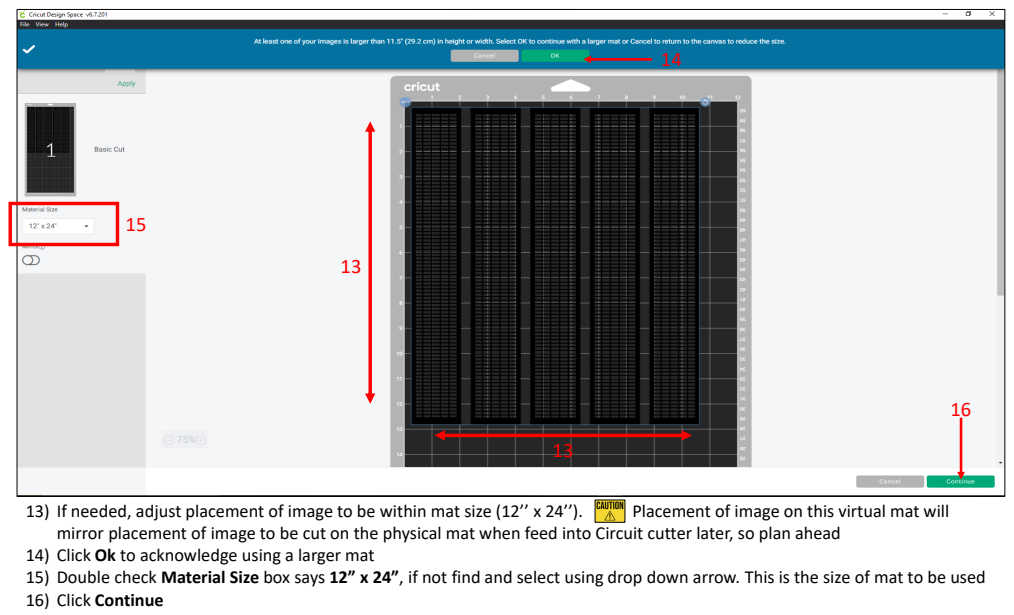
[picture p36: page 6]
13) If needed, adjust placement of image to be within mat size (12’’ x 24’’).; Placement of image on this virtual mat will

mirror placement of image to be cut on the physical mat when feed into Circuit cutter later, so plan ahead
14) Click Ok to acknowledge using a larger mat
15) Double check Material Size box says 12” x 24”, if not find and select using drop down arrow. This is the size of mat to be used
16) Click Continue

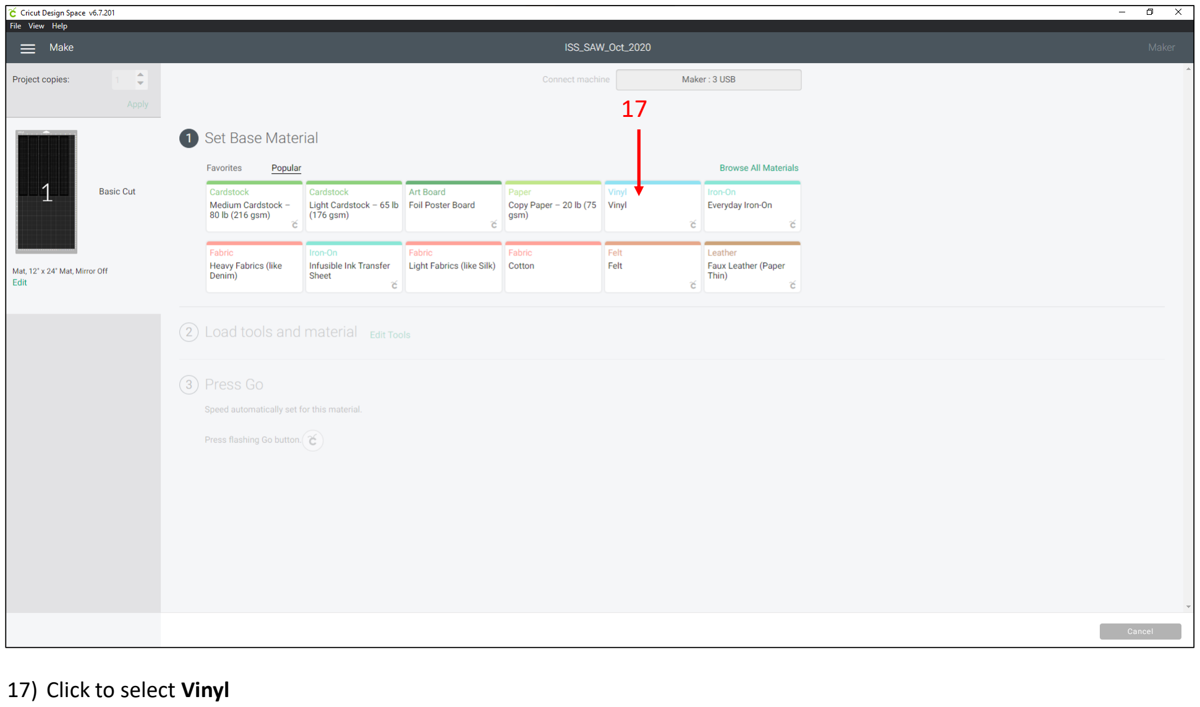
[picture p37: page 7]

17) Click to select Vinyl

17

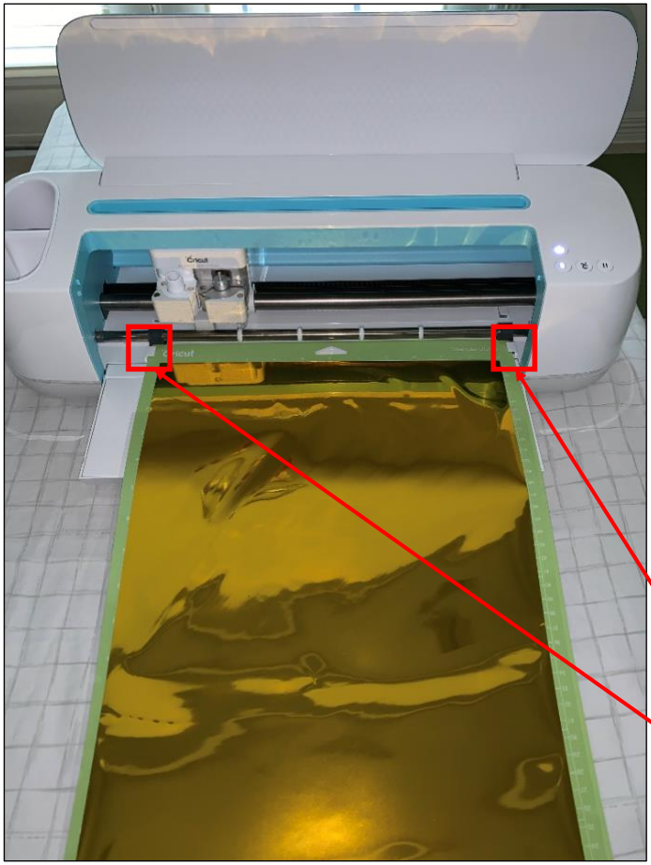
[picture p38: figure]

18) Cricut unit placement : Allow at least 24” of space between back of unit to any object, such as a wall. This is needed to accommodate the physical mat travel space as it cuts the image
19) Prep & load the Vinyl & mat:
- Remove the clear protective film from 12”x24” mat & save for later use). Place the mat on a flat surface, sticky side up
- Unroll the Vinyl sheet, with shiny side up (as shown image to left), align & place the Vinyl sheet onto sticky side of mat. Placing Vinyl sheet on mat can be tricky, easier with a second set of hands, go find a volunteer! Be sure the Vinyl sheet covers the surface area on mat shown as preview in step 13
- If needed, to adjust Vinyl placement on mat, Flip mat onto a flat surface, Vinyl side down. Carpeted floor works just fine. Secure the Vinyl with one hand flat against surface, peel mat slowly from Vinyl with the other hand (instead of Vinyl from mat, this will result in less curl up Vinyl)
- When ready, peel off clear protective film from Vinyl sheet & trash
- Load mat onto Cricut mat track

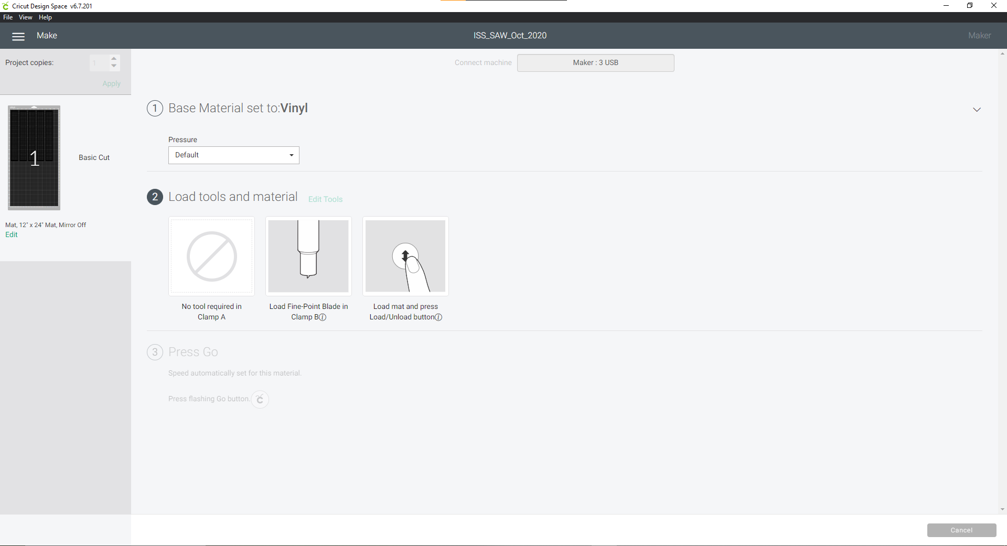
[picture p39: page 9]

20) Check to make sure Fine-Point Blade is in Clamp B. (Pre-install in unit out of box)
21) Press Load button on the Cricut unit. Button should be flashing

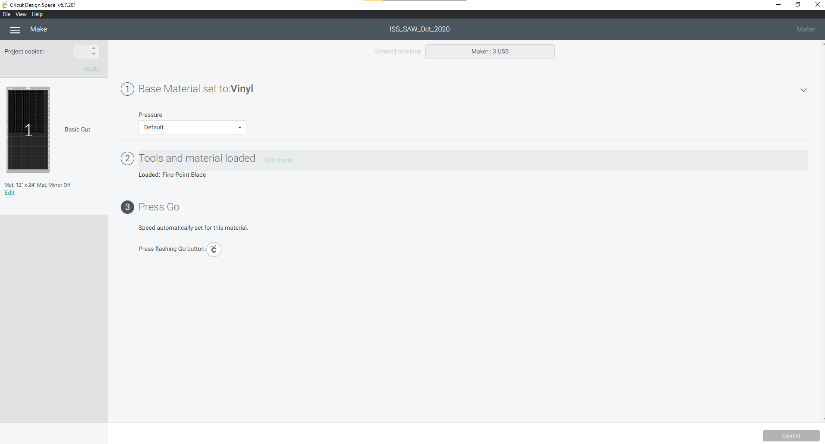
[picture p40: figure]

22) Press Go Cricut button on the Cricut unit. Button should be flashing

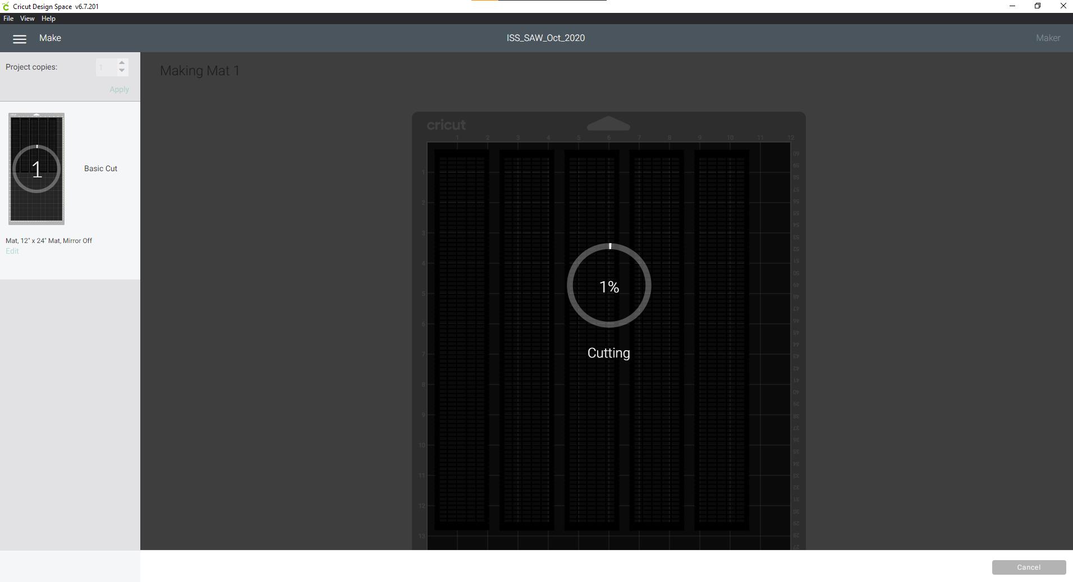
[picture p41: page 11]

23) Sit back and enjoy the cutting show. Take some time to stretch your fingers in readiness for weeding later ;-)

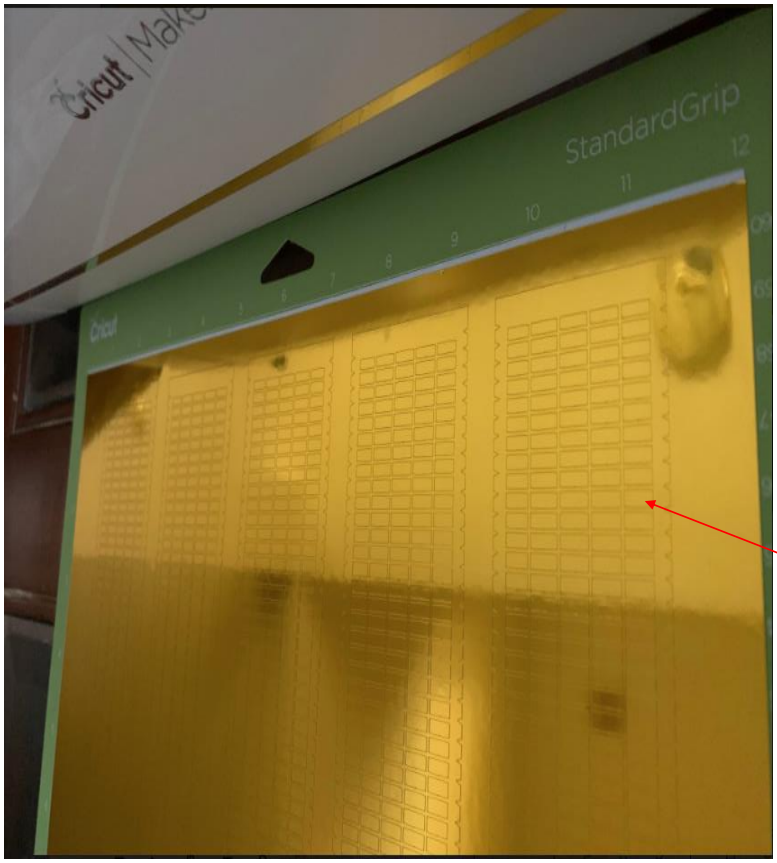
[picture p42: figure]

24) Final Vinyl product looks something like this after cut is complete
25) Release the Vinyl from mat:
- Remove mat from Cricut unit
- Flip mat onto a flat surface, Vinyl side down. Carpet floor works just fine. Secure Vinyl with one hand flat against surface, peel mat slowly from Vinyl with the other hand (instead of Vinyl from mat, this will result in less curl up Vinyl)
26) Using scissors or a paper cutter to cut SAW section from Vinyl roll, set aside for weeding step
27) For time savings, cut next sheet by repeating steps 17 - 26. If complete for the day, place protective sheet back onto sticky side of mat. This will extend life of the mat
28) Weeding the Vinyl sheet (do while next sheet is being cut or save for later. Your favorite beverage is recommend for this task ;-)
- Place the cut SAW Vinyl on a flat solid surface, such as a clip board, counter top or desk. I used a large clip board of sort, friendlier on the neck and the back
- Use an embossing tool or weeding tool to pick and remove each small tiny rectangles. The tiny rectangles are to be trashed, but the delicate outlines are kept, so be careful not to damage them
- When using an embossing tool, firmly press the balled point from the corner of a tiny rectangle & push up to release the adhesive back from the backing sheet. Use tweezers or fingers to remove tiny rectangles, and trash. Yes! There are a lot of them, all rectangles will need to be removed

29) Cut transfer tape from roll, it needs to be slightly larger than the Vinyl cut. The extra transfer tape will allow handling of the Vinyl onto 3D print later and easier removal of the transfer tape from Vinyl afterwards
30) Place transfer tape onto Vinyl, sticky side of transfer tape onto shiny side of Vinyl. Press down for good contact
31) Flip the whole thing over, transfer tape down, Vinyl backing sheet up. Pin transfer tape against flat surface with one hand, peel back Vinyl sheet to remove from transfer tape. Vinyl backing sheet will be completely removed, outer edges of the shiny Vinyl will be removed too. Once done, you will noticed, the sticky sides of the transfer tape and Vinyl are on the same side, one big sticker
32) For easier application of Vinyl to 3D print, cut transfer tape between the images to free each SAW outline from the group

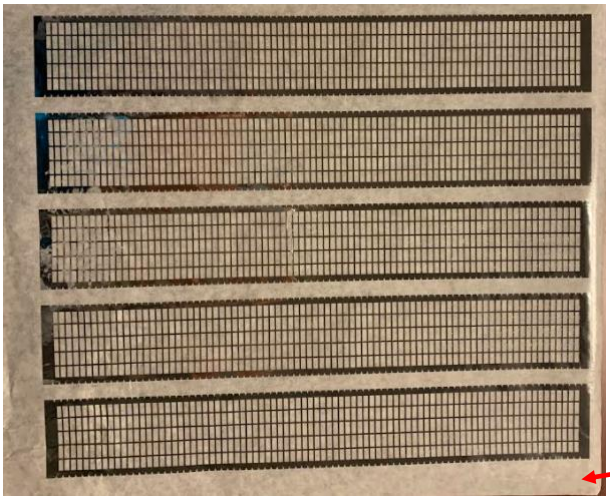
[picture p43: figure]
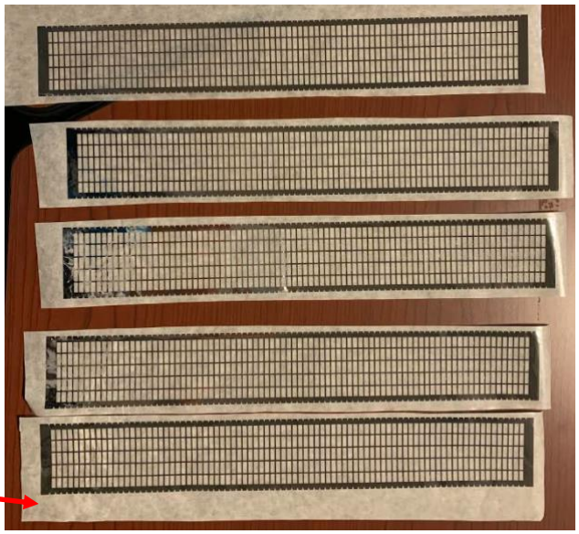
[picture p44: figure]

Transfer tape

After tiny
rectangles are
removed + onto
transfer paper

Cut

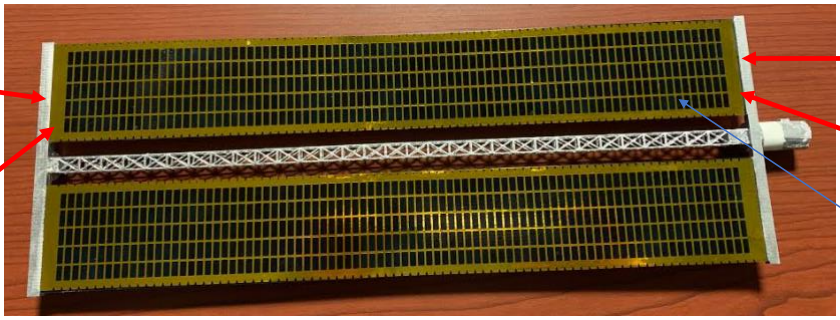
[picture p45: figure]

33) Transfer the Vinyl onto 3D print (blue side). Place a SAW Vinyl sticker sticky side up, horizontally on a flat surface
34) Holding 3D printed SAW with both hands horizontally, blue side down, align the blue edges of 3D print to be the edges of shiny Vinyl. Vinyl edges should just touching the silver areas, covering all the blue painted area of the 3D print
35) Once aligned, lower the 3D print onto Vinyl sticker. Flip 3D print over to check alignment. If adjustment is needed, peel the sticker off 3D print, and try again until alignment is properly done. (Backup vinyl panel is available if needed)
36) When ready, to secure adhesive to 3D print simply place the 3D print with Vinyl/transfer tape side down back onto a flat surface, use fingers, hand or under side of a fist to press down on 3D print to encourage better adhesion of Vinyl to 3D print
37) To remove transfer tape from Vinyl, flip the 3D print over with truss down (aka, transfer tape up)
38) Peel transfer tape off Vinyl, start from a corner, pull slowly at a 45 degree angle to peel transfer tape away from the Vinyl. Its useful to keep one hand on Vinyl against 3D print while the other hand pull transfer tape away (this is not a ban-aide, don’t rip it off fast, slow is the key)
39) Once complete, Vinyl will stay on the 3D print, transfer tape can be trashed. ISS panel would look like the above image

Silver edge of
3D print

Silver edge of
3D print

Gold edge of
Vinyl

Gold edge of
Vinyl

Blue painted area
of 3D print

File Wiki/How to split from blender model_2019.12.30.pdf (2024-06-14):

1. Open ISS Blender File. Can be downloaded here: https://nasa3d.arc.nasa.gov/detail/iss
2. While in Object Mode (located lower left)

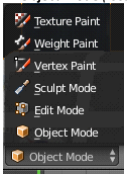
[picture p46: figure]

Start: 0.100 (default)
End: 100,000
3. Extend Clipping distance as follows, then hit ENTER button or click away from box

File -> User Preferences -> Input -> check "Emulate 3 button Mouse" -> Save User Settings Same can be done with "Emulate Numpad"

Click and hold middle mouse button to spin model. Click axis arrow then slid up/down/side to move model left, right, up or down. If middle mouse button is not available, you can Emulate 3 button Mouse by following these settings…

4.

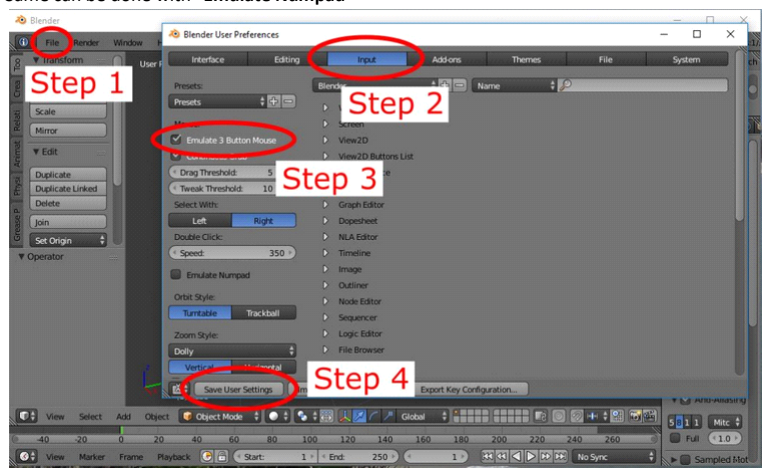
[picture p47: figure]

5. Locate piece of ISS to split

# How to split from blender model

Monday, December 30, 2019 12:14 PM

New Section 1 Page 1

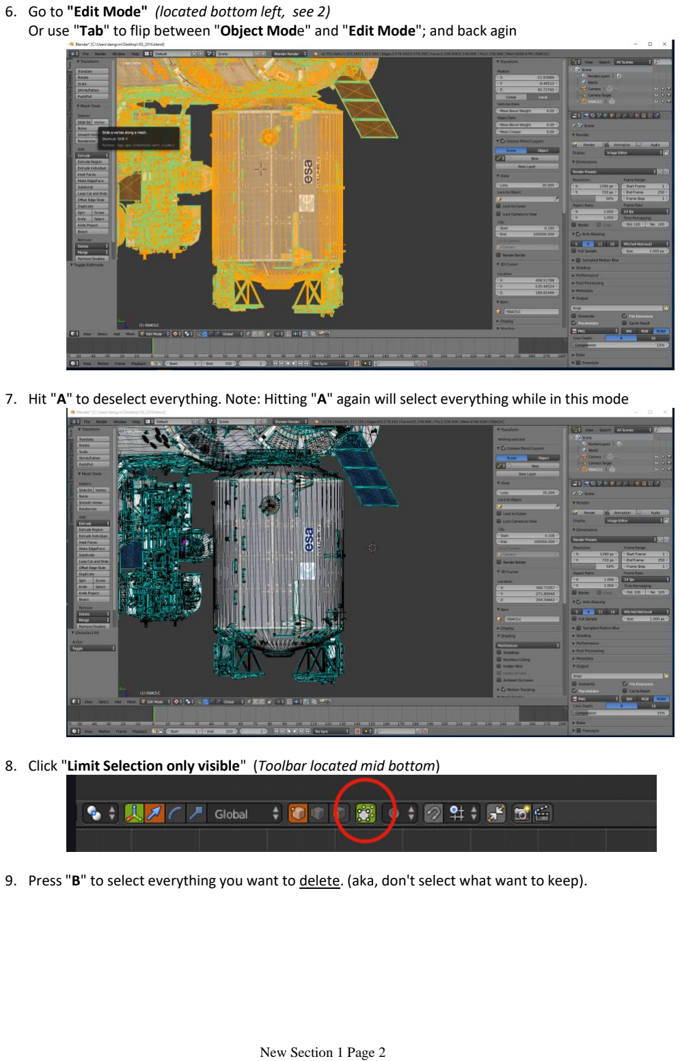
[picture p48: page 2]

6. Go to "Edit Mode" (located bottom left, see 2)
Or use "Tab" to flip between "Object Mode" and "Edit Mode"; and back agin
7. Hit "A" to deselect everything. Note: Hitting "A" again will select everything while in this mode
8. Click "Limit Selection only visible" (Toolbar located mid bottom)
9. Press "B" to select everything you want to delete. (aka, don't select what want to keep).

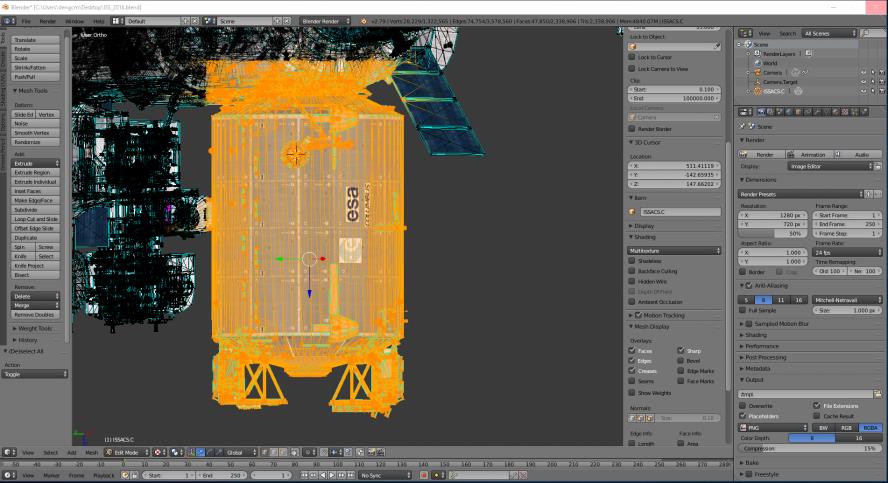
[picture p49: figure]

10. Press "X" to bring up the delete menu; then click "Vertices"

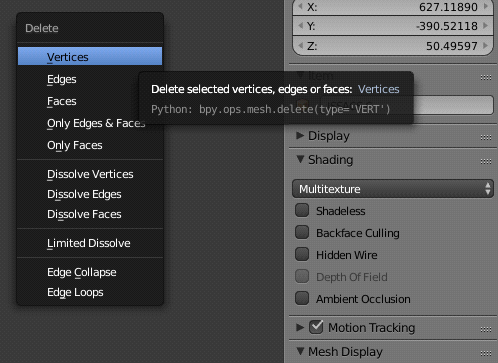
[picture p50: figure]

11. Repeat delete area until only the desire model piece wanted for printing remains

Note: If cursor has issues (aka, locked curser), pressing L while over something will select everything attached to whatever your cursor is over (but it’s a bit non precise, sometimes it will just jump to nearby faces). If it ever selects the wrong stuff, pressing A will unselect everything.
Note: Number pad 5 & then Number pad 1 will take you center to model if you get lost in the margin Note: Number pad "." will take you back to center of model

File -> Export STL
Select "Ascii" check box (left bottom ish)
Just above "Ascii", click Scale, then type in "0.0254" At top, title it, then click "Export STL" upper right
12. Saving file to STL format for printing:

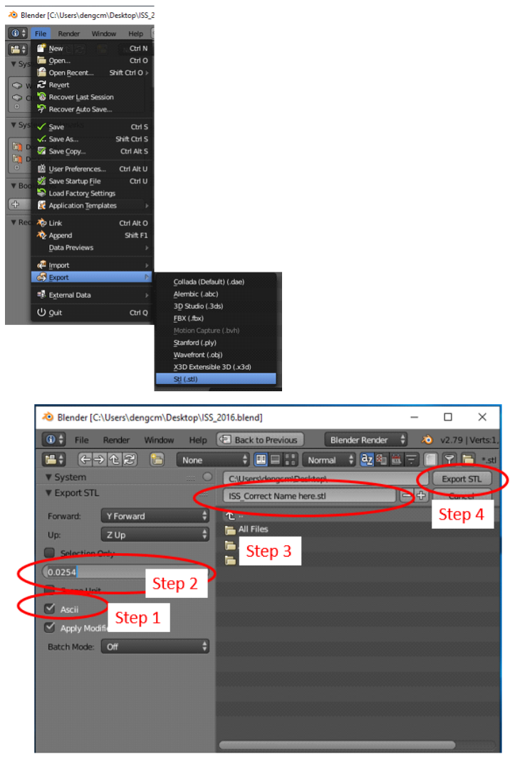
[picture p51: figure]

(Note: Scale display only display up to 2 decimal. So you will notice it will auto change to '0.03' after input of '0.0254'. Know that Blender will still apply the '0.0254' factor)

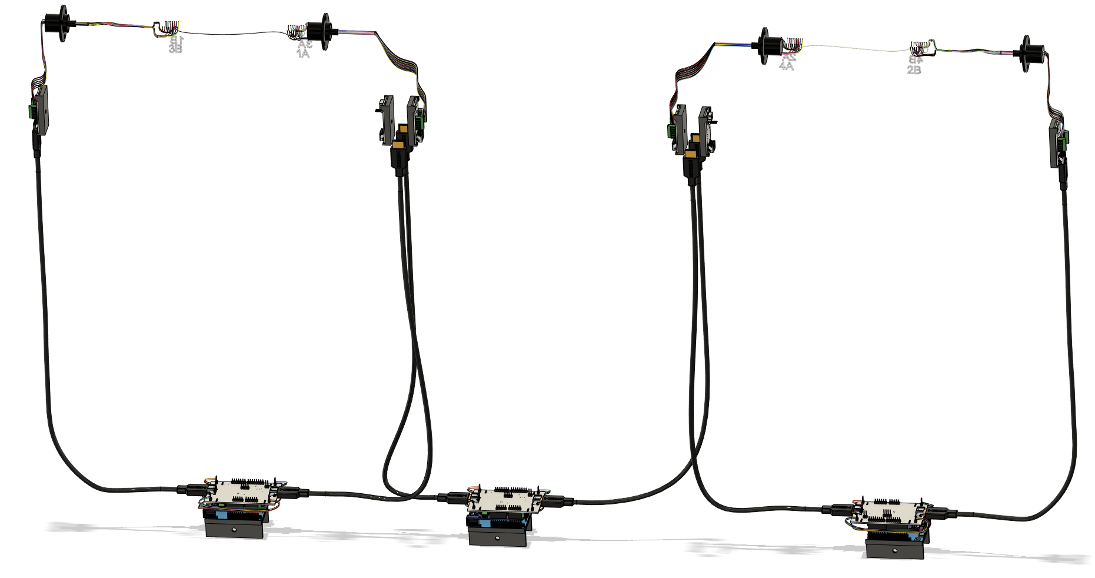
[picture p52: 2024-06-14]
Wiki/Images/Mimic_Wiring.png

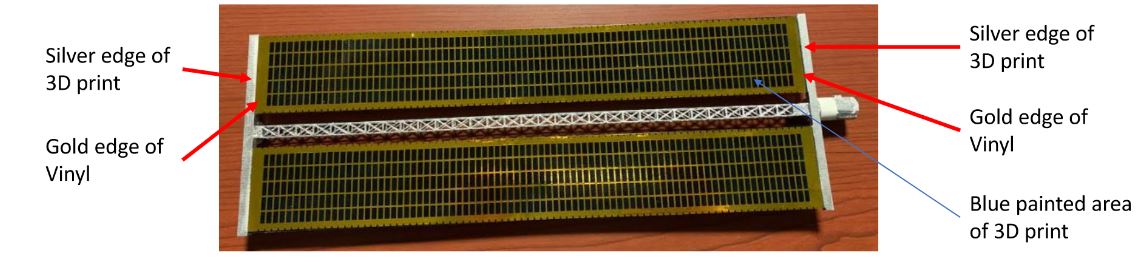
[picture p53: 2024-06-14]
Wiki/Images/VinylInstalledOnSaw.JPG

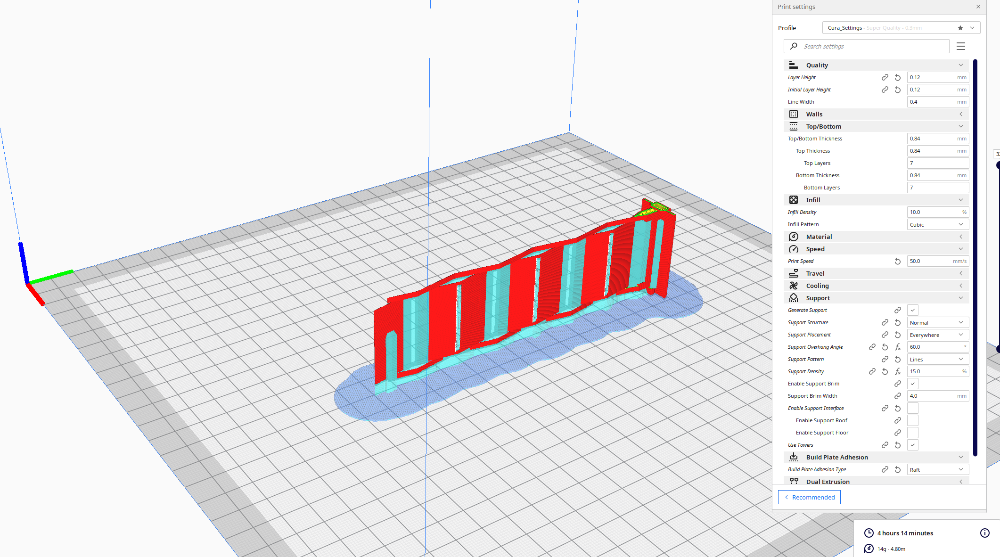
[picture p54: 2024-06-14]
3D_Printing/PV_Radiator/image.png

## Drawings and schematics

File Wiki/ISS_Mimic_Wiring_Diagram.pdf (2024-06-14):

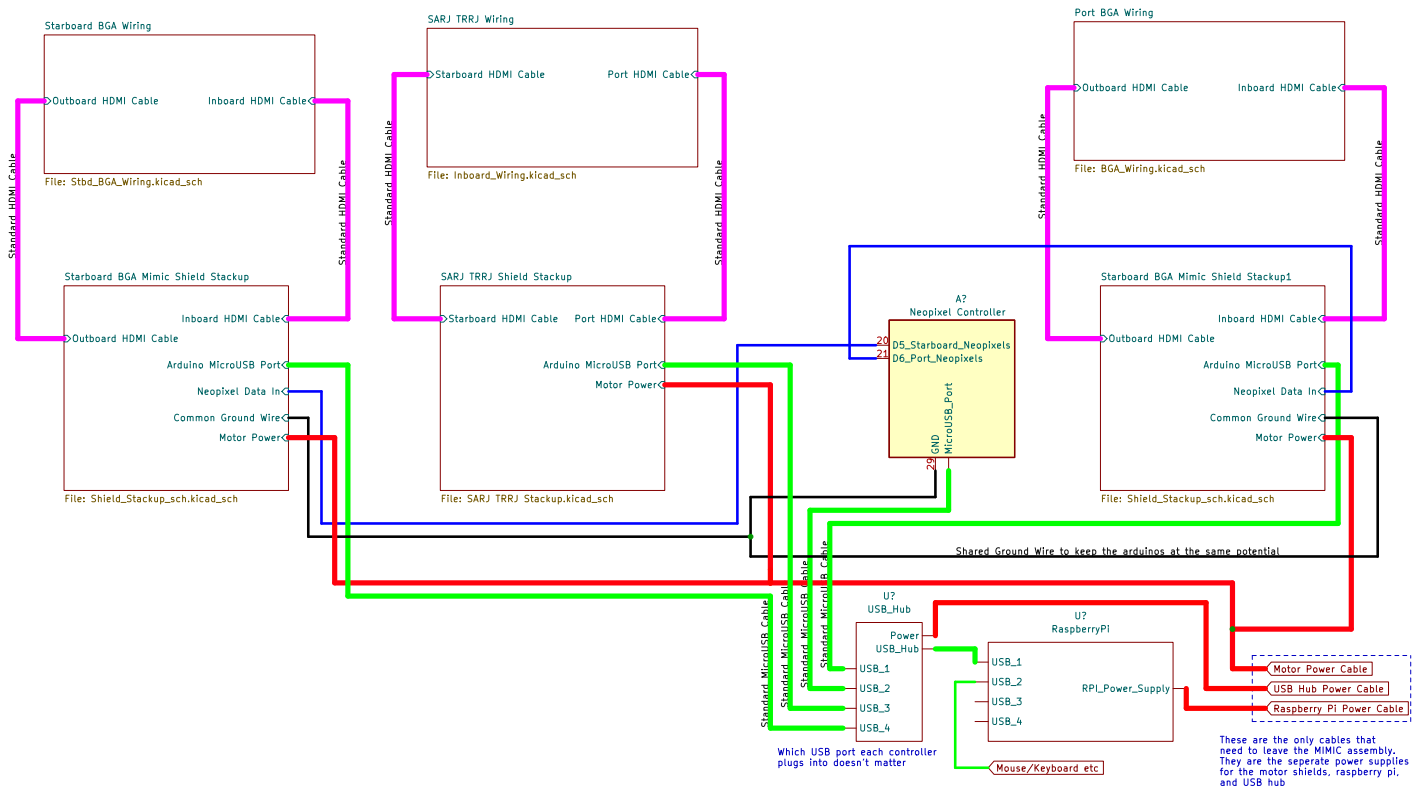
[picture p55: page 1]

Inboard HDMI Cable Arduino MicroUSB Port Starboard BGA Mimic Shield Stackup

Inboard HDMI Cable Arduino MicroUSB Port Starboard BGA Mimic Shield Stackup1

Neopixel Data In Outboard HDMI Cable

Shared Ground Wire to keep the arduinos at the same potential

These are the only cables that
need to leave the MIMIC assembly.
They are the seperate power supplies
for the motor shields, raspberry pi, and USB hub

Which USB port each controller
plugs into doesn't matter

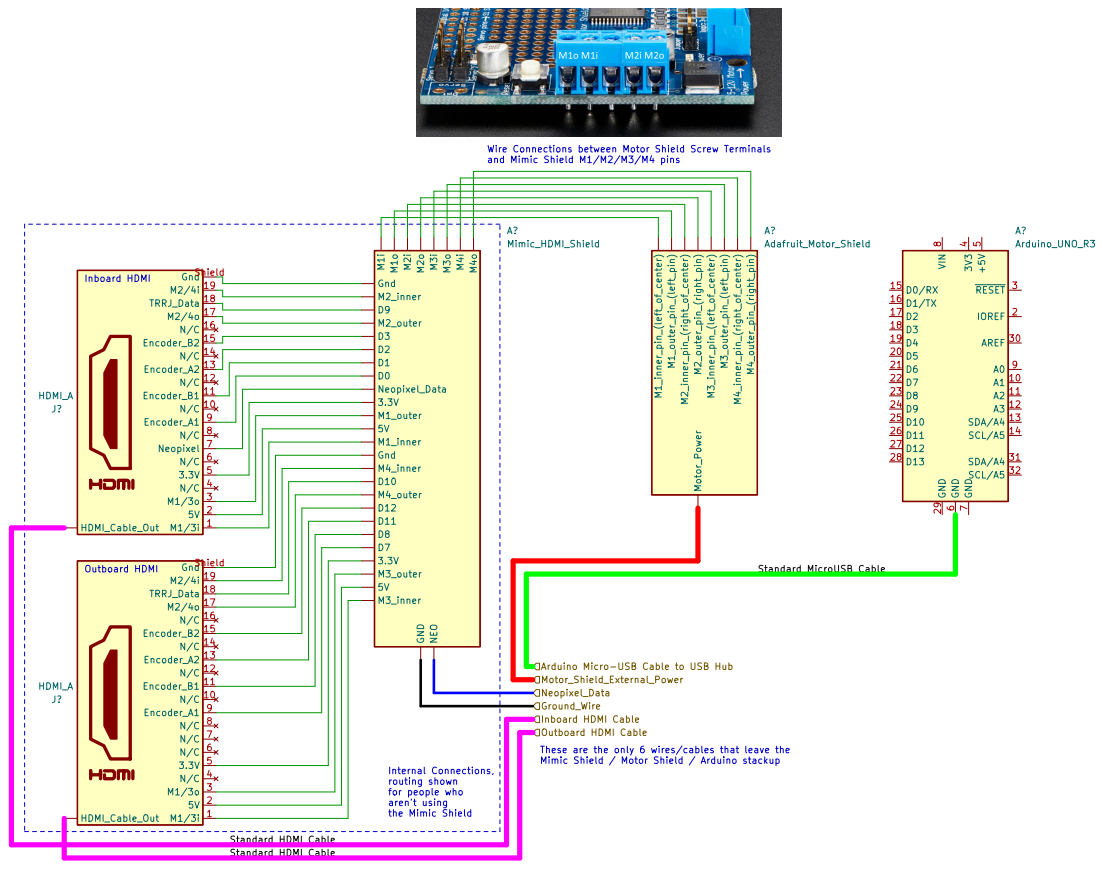
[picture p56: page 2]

Mimic Shield / Motor Shield / Arduino stackup

Internal Connections, routing shown

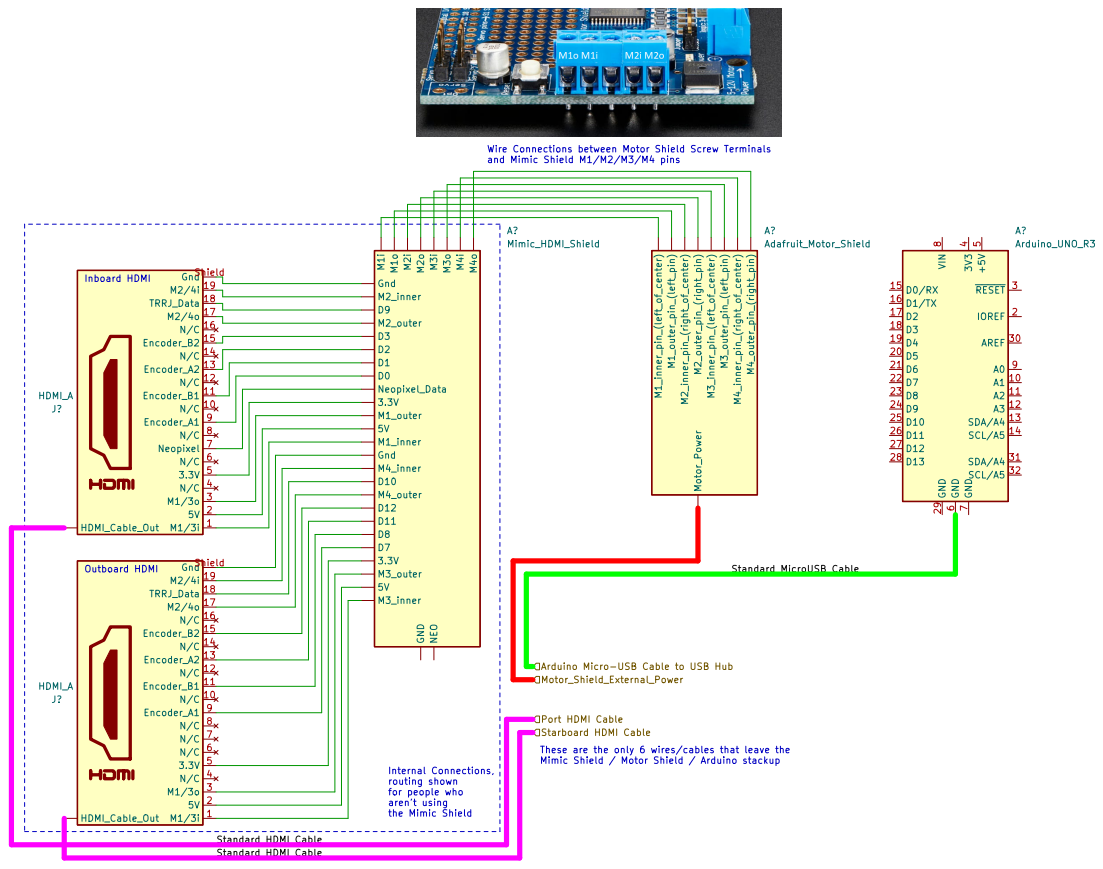
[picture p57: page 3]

8 A0 9A?Arduino_UNO_R3 Motor_Shield_External_Power Starboard HDMI Cable Port HDMI Cable Arduino Micro-USB Cable to USB Hub Standard HDMI Cable Standard HDMI Cable Standard MicroUSB Cable Wire Connections between Motor Shield Screw Terminals and Mimic Shield M1/M2/M3/M4 pins

Inboard HDMI Outboard HDMI

Mimic Shield / Motor Shield / Arduino stackup

Internal Connections, routing shown

Mimic Shield / Motor Shield / Arduino stackup

Internal Connections, routing shown

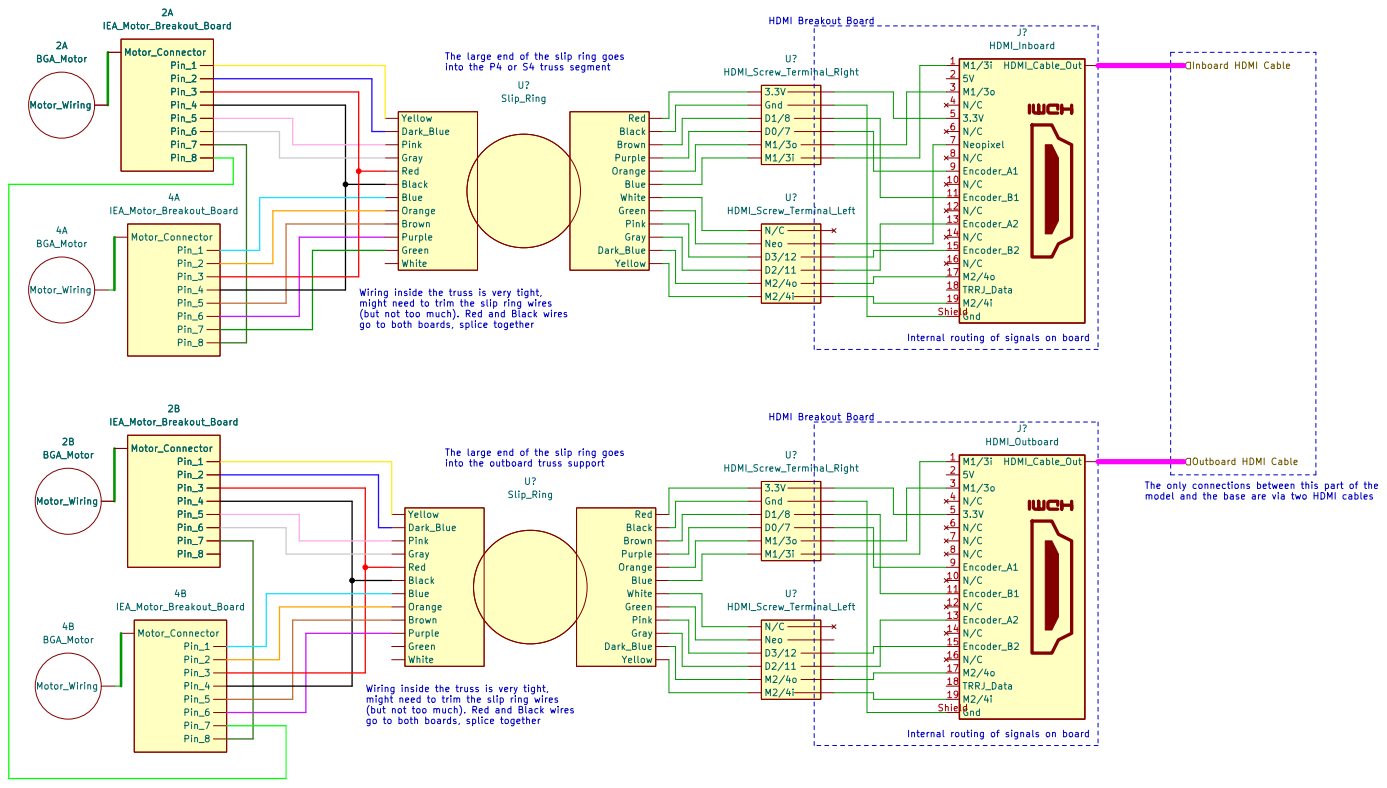
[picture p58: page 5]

HDMI Breakout Board Wiring inside the truss is very tight,

The large end of the slip ring goes
into the P4 or S4 truss segment

Inboard HDMI Cable Outboard HDMI Cable

might need to trim the slip ring wires
(but not too much). Red and Black wires

go to both boards, splice together 2B

Internal routing of signals on board HDMI Breakout Board

into the outboard truss support

The only connections between this part of the model and the base are via two HDMI cables

Wiring inside the truss is very tight,
go to both boards, splice together

Internal routing of signals on board

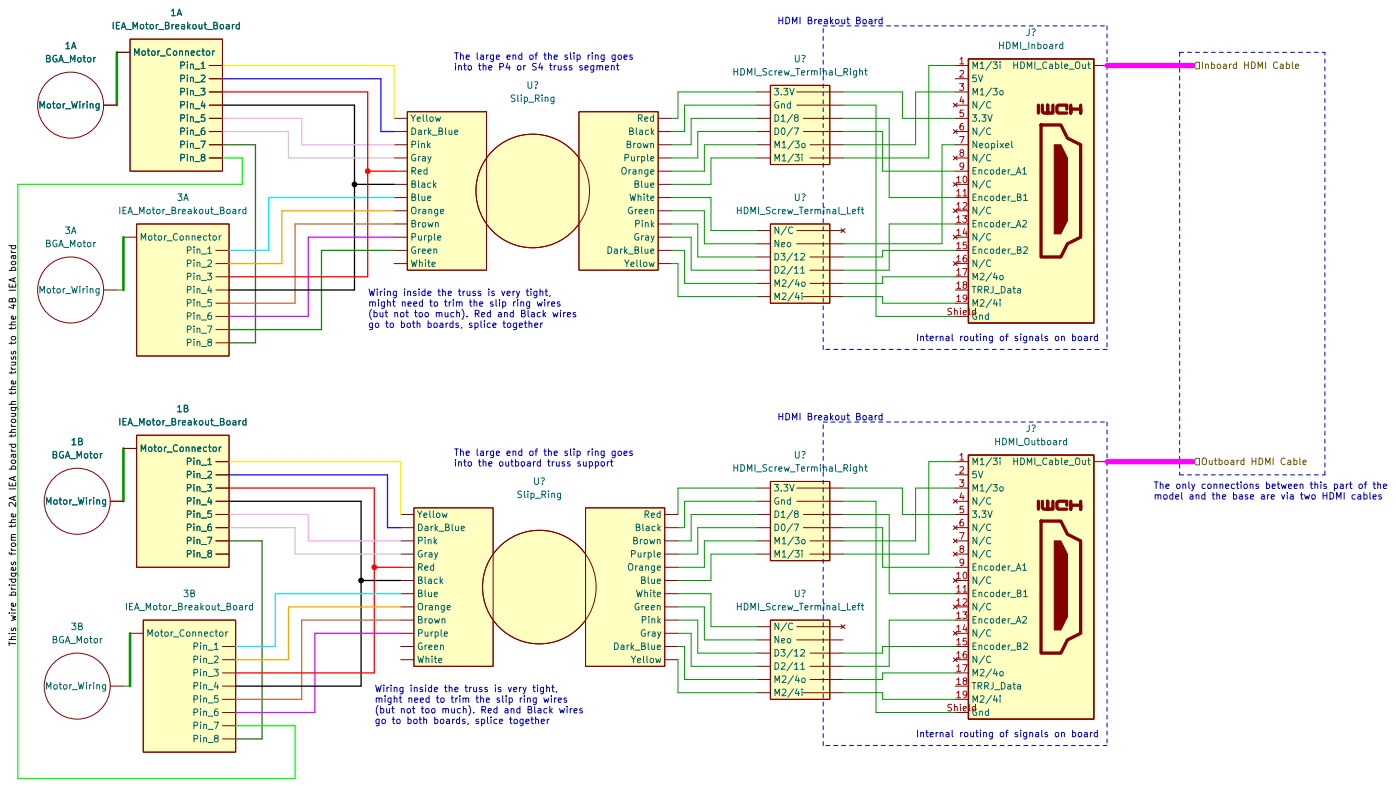
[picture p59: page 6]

The large end of the slip ring goes

Inboard HDMI Cable Outboard HDMI Cable This wire bridges from the 2A IEA board through the truss to the 4B IEA board

Wiring inside the truss is very tight,
might need to trim the slip ring wires
(but not too much). Red and Black wires

Internal routing of signals on board

into the outboard truss support

The only connections between this part of the model and the base are via two HDMI cables Wiring inside the truss is very tight,

go to both boards, splice together

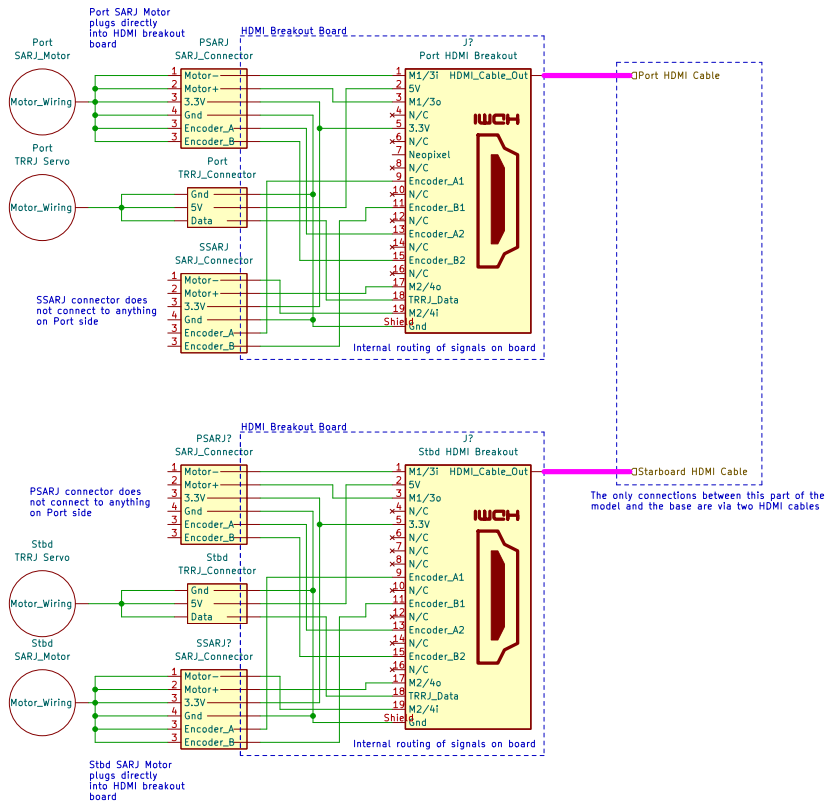
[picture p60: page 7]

Port SARJ Motor plugs directly

J? Port HDMI Breakout
on Port side Stbd SARJ Motor plugs directly
into HDMI breakout board PSARJ connector does not connect to anything

Internal routing of signals on board

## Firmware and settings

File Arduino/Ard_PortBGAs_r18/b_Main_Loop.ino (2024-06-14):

void loop() {


  bga_2B.PosCmd = B2B; // From RasPi telemetry stream
  bga_2A.PosCmd = B2A; // From RasPi telemetry stream
  bga_4B.PosCmd = B4B; // From RasPi telemetry stream
  bga_4A.PosCmd = B4A; // From RasPi telemetry stream

  if (NULLIFY == 1) {
    digitalWrite(13, LOW);
    delay(500);
    motorNULL(bga_2B);    myEnc2B.write(0); B2B = 0;

    motorNULL(bga_2A);     myEnc2A.write(0); B2A = 0;

    motorNULL(bga_4B);     myEnc4B.write(0); B4B = 0;

    motorNULL(bga_4A);    myEnc4A.write(0); B4A = 0;

    digitalWrite(13, HIGH);
    digitalWrite(6, LOW);
    delay(500);
    NULLIFY = 0;
    digitalWrite(6, HIGH);

  }

  // Can likely simplify this, but need to incorporate Adafruit motor shield library commands into my motor function/struct

  motorfnc(bga_2B); // this is where it's called
  if (bga_2B.tmpSpeed > 0) {
    myMotorB2B->run(FORWARD); // This command is necessary for the AdaFruit boards, requiring conditionals (rather than signed speeds taking care of direction).
  }
  else {
    myMotorB2B->run(BACKWARD);
  }
  myMotorB2B->setSpeed(bga_2B.CmdSpeed);// + 20);

  motorfnc(bga_4B); // this is where it's called
  if (bga_4B.tmpSpeed > 0) {
    myMotorB4B->run(FORWARD); // This command is necessary for the AdaFruit boards, requiring conditionals (rather than signed speeds taking care of direction).
  }
  else {
    myMotorB4B->run(BACKWARD);
  }
  myMotorB4B->setSpeed(bga_4B.CmdSpeed);// + 20);


  motorfnc(bga_2A); // this is where it's called
  if (bga_2A.tmpSpeed > 0) {
    myMotorB2A->run(FORWARD); // This command is necessary for the AdaFruit boards, requiring conditionals (rather than signed speeds taking care of direction).
  }
  else {
    myMotorB2A->run(BACKWARD);
  }
  myMotorB2A->setSpeed(bga_2A.CmdSpeed);// + 20);


  motorfnc(bga_4A); // this is where it's called
  if (bga_4A.tmpSpeed > 0) {
    myMotorB4A->run(FORWARD); // This command is necessary for the AdaFruit boards, requiring conditionals (rather than signed speeds taking care of direction).
  }
  else {
    myMotorB4A->run(BACKWARD);
  }
  myMotorB4A->setSpeed(bga_4A.CmdSpeed);// + 20);



  D0 = digitalRead(0);
  D1 = digitalRead(1);
  D2 = digitalRead(2);
  D3 = digitalRead(3);
  //  D4 = digitalRead(4);
  //  D5 = digitalRead(5);
  //  D6 = digitalRead(6);
  D7 = digitalRead(7);
  D8 = digitalRead(8);
  //  D9= digitalRead(9);
  //  D10= digitalRead(10);
  D11 = digitalRead(11);
  D12 = digitalRead(12);
  //D13 = digitalRead(13);
  ////D14 = digitalRead(14);
  D15 = digitalRead(15);
  D16 = digitalRead(16);
  D17 = digitalRead(17);



  delay(1);
  if (Serial.available())
  {
    checkSerial();
  }

  int  debug_mode = 8;

  delay(1);

  // ============== Time measures ===================================================
  LoopStartMillis = millis();
  delta_t_millis = max(LoopStartMillis - previousMillis, 1); // ensure always equal to at least one, for later inversion
  inverse_delta_t_millis = 1 / ((float) delta_t_millis); // BCM mod 10/28/2018: for some reason, was not inverted (just = value, rather than 1/value).
  millisChPt1 = millis() - LoopStartMillis;
  // ================================================================================

  bga_2A.Count = myEnc2A.read();
  bga_4A.Count = myEnc4A.read();
  bga_2B.Count = myEnc2B.read();
  bga_4B.Count = myEnc4B.read();

  millisChPt2 = millis() - LoopStartMillis;

  if (debug_mode == 8) {
    Serial.print("|  ");

    Serial.print("Count_B2A: ");
    Serial.print(bga_2A.Count);
    Serial.print(",Count_B4A: ");
    Serial.print(bga_4A.Count);
    Serial.print("Count_B2B: ");
    Serial.print(bga_2B.Count);
    Serial.print(",Count_B4B: ");
    Serial.print(bga_4B.Count);
    Serial.print(",SmartRolloverBGA");
    Serial.print(SmartRolloverBGA);

    Serial.print(",D0:");
    Serial.print(D0);
    Serial.print(",D1:");
    Serial.print(D1);
    Serial.print(",D2:");
    Serial.print(D2);
    Serial.print(",D3:");
    Serial.print(D3);
    //    Serial.print(",D4:");
    //    Serial.print(D4);
    //    Serial.print(",D5: ");
    //    Serial.print(D5);
    //    Serial.print(",D6:");
    //    Serial.print(D6);
    Serial.print(",D7: ");
    Serial.print(D7);
    Serial.print(",D8:");
    Serial.print(D8);

    //    Serial.print(",D9: ");
    //    Serial.print(D9);
    //        Serial.print(",D10:");
    //        Serial.print(D10);

    Serial.print(",D11: ");
    Serial.print(D11);
    Serial.print(",D12: ");
    Serial.print(D12);
    //    Serial.print(",D13: ");
    //  Serial.print(D13);
    Serial.print(",D14: ");
    Serial.print(D14);
    Serial.print(",D15: ");
    Serial.print(D15);
    Serial.print(",D16: ");
    Serial.print(D16);
    Serial.print(",D17: ");
    Serial.print(D17);

    Serial.print("| PosErrs ");
    Serial.print(bga_2A.PosErr);
    Serial.print(", ");
    Serial.print(bga_4A.PosErr);
    Serial.print(", ");
    Serial.print(bga_2B.PosErr);
    Serial.print(", ");
    Serial.print(bga_4B.PosErr);
    //    Serial.print(", ");
    //    Serial.print(PosErr_PSARJ);
    //    Serial.print(", ");
    //    Serial.print(PosErr_SSARJ);
    //
    //    Serial.print(", ");
    //    Serial.print("Integer Mtr Spd Cmd to Shield(PortSrj):");
    //    Serial.print(CmdSpeed_PSARJ);
    //Serial.print(PosErr_SSARJ);
    Serial.println("|  ");
  }

  previousMillis = LoopStartMillis;

  millisChPt6 = millis() - LoopStartMillis;

  delay(3);
}

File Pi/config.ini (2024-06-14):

[kivy]
keyboard_repeat_delay = 300
keyboard_repeat_rate = 30
log_dir = logs
log_enable = 1
log_level = info
log_name = kivy_%y-%m-%d_%_.txt
window_icon = 
keyboard_mode = 
keyboard_layout = qwerty
desktop = 1
exit_on_escape = 1
pause_on_minimize = 0
kivy_clock = default
default_font = ['Roboto', 'data/fonts/Roboto-Regular.ttf', 'data/fonts/Roboto-Italic.ttf', 'data/fonts/Roboto-Bold.ttf', 'data/fonts/Roboto-BoldItalic.ttf']
log_maxfiles = 100
window_shape = data/images/defaultshape.png
config_version = 24

[graphics]
display = -1
fullscreen = 1
height = 480
left = 0
maxfps = 60
multisamples = 2
position = auto
rotation = 0
show_cursor = 1
top = 0
width = 800
resizable = 0
borderless = 1
window_state = visible
minimum_width = 0
minimum_height = 0
min_state_time = .035
allow_screensaver = 0
shaped = 0
vsync = 
verify_gl_main_thread = 1
custom_titlebar = 0
custom_titlebar_border = 5

[input]
mouse = mouse
#mtdev_%(name)s = probesysfs,provider=mtdev
hid_%(name)s = probesysfs,provider=hidinput

[postproc]
double_tap_distance = 20
double_tap_time = 250
ignore = []
jitter_distance = 0
jitter_ignore_devices = mouse,mactouch,
retain_distance = 50
retain_time = 0
triple_tap_distance = 20
triple_tap_time = 375

[widgets]
scroll_timeout = 250
scroll_distance = 20
scroll_friction = 1.
scroll_stoptime = 300
scroll_moves = 5

[modules]

[network]
useragent = curl

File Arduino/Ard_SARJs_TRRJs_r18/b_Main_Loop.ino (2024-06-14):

void loop() {



  sarj_port.PosCmd = PSARJ; // From RasPi telemetry stream
  sarj_stbd.PosCmd = SSARJ; // From RasPi telemetry stream


  if (NULLIFY == 1) {
    motorNULL(sarj_port); myEncPSARJ.write(0); PSARJ = 0;
    motorNULL(sarj_stbd); myEncSSARJ.write(0); SSARJ = 0;
    NULLIFY = 0;
  }

  // Can likely simplify this, but need to incorporate Adafruit motor shield library commands into my motor function/struct

  motorfnc(sarj_port); // this is where it's called
  if (sarj_port.tmpSpeed > 0) {
    myMotorPSARJ->run(FORWARD); // This command is necessary for the AdaFruit boards, requiring conditionals (rather than signed speeds taking care of direction).
  }
  else {
    myMotorPSARJ->run(BACKWARD);
  }
  myMotorPSARJ->setSpeed(sarj_port.CmdSpeed);// + 20);

  motorfnc(sarj_stbd); // this is where it's called
  if (sarj_stbd.tmpSpeed > 0) {
    myMotorSSARJ->run(FORWARD); // This command is necessary for the AdaFruit boards, requiring conditionals (rather than signed speeds taking care of direction).
  }
  else {
    myMotorSSARJ->run(BACKWARD);
  }
  myMotorSSARJ->setSpeed(sarj_stbd.CmdSpeed);// + 20);


  D0 = digitalRead(0);
  D1 = digitalRead(1);
  D2 = digitalRead(2);
  D3 = digitalRead(3);
  D4 = digitalRead(4);
  D5 = digitalRead(5);
  D6 = digitalRead(6);
  D7 = digitalRead(7);
  D8 = digitalRead(8);
  D9 = digitalRead(9);
  D10 = digitalRead(10);
  D11 = digitalRead(11);
  D12 = digitalRead(12);
  D13 = digitalRead(13);
  D14 = digitalRead(14);
  D15 = digitalRead(15);
  D16 = digitalRead(16);
  D17 = digitalRead(17);

  delay(1);
  if (Serial.available())
  {
    checkSerial();
  }

  int  debug_mode = 8;
  //  B2A = 100 + 90.0* sin(2.0 * 3.14159 * 0.01 * millis() / 1000.0);
  //  B4A = 100 + 90.0* sin(2.0 * 3.14159 * 0.01 * millis() / 1000.0);
  //  B2B = 100 + 90.0* sin(2.0 * 3.14159 * 0.01 * millis() / 1000.0);
  //  B4B = 100 + 90.0* sin(2.0 * 3.14159 * 0.01 * millis() / 1000.0);
  //  PTRRJ=104*sin(1*3.14159*0.01*millis()/1000.0);


  // ========= Servo Stuff =============================
  // For TRRJ's, it's most important to get cleanly to zero and be able to achieve 90 deg for storage. Have to make some minor code modifications since the physical tooth locations on the servos/horns may not line up with zero.

  // Saturating at 90 deg rather than scaling input, since TRRJ rarely moves past 90 deg anyway.
  PTRRJ = max(PTRRJ, -120); // saturate at -90 deg, but servo needs to be pushed a bit higher than that.
  PTRRJ = min(PTRRJ, 120); // saturate at 90 deg
  //servo_PTRRJ.write(-1*PTRRJ);
  servo_PTRRJ.write(map(-1 * (PTRRJ - 15), -90, 90, -10, 190)); // 90 deg cmd is a little short, so bumping to 95 deg


  STRRJ = max(STRRJ, -120); // saturate at -90 deg
  STRRJ = min(STRRJ, 120); // saturate at 90 deg
  //servo_STRRJ.write(-1*STRRJ);
  servo_STRRJ.write(map(-1 * (STRRJ - 12), -90, 90, -15, 195)); // 90 deg cmd is a little short, so bumping to 95 deg
  //servo_STRRJ.write(map(-1*(STRRJ), -90, 90, 0, 180)); // 90 deg cmd is a little short, so bumping to 95 deg

  delay(1);
  // ========= END Servo Stuff============================

  // ============== Time measures ===================================================
  LoopStartMillis = millis();
  delta_t_millis = max(LoopStartMillis - previousMillis, 1); // ensure always equal to at least one, for later inversion
  inverse_delta_t_millis = 1 / ((float) delta_t_millis); // BCM mod 10/28/2018: for some reason, was not inverted (just = value, rather than 1/value).
  millisChPt1 = millis() - LoopStartMillis;
  // ================================================================================


  sarj_port.Count = myEncPSARJ.read();
  sarj_stbd.Count = myEncSSARJ.read();

  //
  millisChPt2 = millis() - LoopStartMillis;


  if (debug_mode == 8) {
    Serial.print("|  ");
    //
    //    Serial.print("Count_B2A: ");
    //    Serial.print(Count_B2A);
    //    Serial.print(",Count_B4A: ");
    //    Serial.print(Count_B4A);
    //    Serial.print("Count_B2B: ");
    //    Serial.print(Count_B2B);
    //    Serial.print(",Count_B4B: ");
    //    Serial.print(Count_B4B);

    Serial.print(",Count_PSARJ: ");
    Serial.print(sarj_port.Count);
    Serial.print(",Count_SSARJ: ");
    Serial.print(sarj_stbd.PosErr);

    Serial.print(",D0:");
    Serial.print(D0);
    Serial.print(",D1:");
    Serial.print(D1);
    Serial.print(",D2:");
    Serial.print(D2);
    Serial.print(",D3:");
    Serial.print(D3);
    //    Serial.print(",D4:");
    //    Serial.print(D4);
    Serial.print(",D5: ");
    Serial.print(D5);
    //    Serial.print(",D6:");
    //    Serial.print(D6);
    Serial.print(",D7: ");
    Serial.print(D7);
    Serial.print(",D8:");
    Serial.print(D8);

    //    Serial.print(",D9: ");
    //    Serial.print(D9);
    //        Serial.print(",D10:");
    //        Serial.print(D10);

    Serial.print(",D11: ");
    Serial.print(D11);
    Serial.print(",D12: ");
    Serial.print(D12);

    Serial.print(",D14: ");
    Serial.print(D14);
    Serial.print(",D15: ");
    Serial.print(D15);
    Serial.print(",D16: ");
    Serial.print(D16);
    Serial.print(",D17: ");
    Serial.print(D17);

    Serial.print("| PosErrs Prt;Stbd: ");

    Serial.print(sarj_port.PosErr);
    Serial.print(", ");
    Serial.print(sarj_stbd.PosErr);
    //    Serial.print(", ");
    Serial.print("| CmdSpd Prt;Stbd: ");
    Serial.print(sarj_port.CmdSpeed);
    Serial.print(", ");
    Serial.print(sarj_stbd.CmdSpeed);

    Serial.println("|  ");

  }

  previousMillis = LoopStartMillis;

  millisChPt6 = millis() - LoopStartMillis;

  delay(3);
}

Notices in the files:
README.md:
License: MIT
